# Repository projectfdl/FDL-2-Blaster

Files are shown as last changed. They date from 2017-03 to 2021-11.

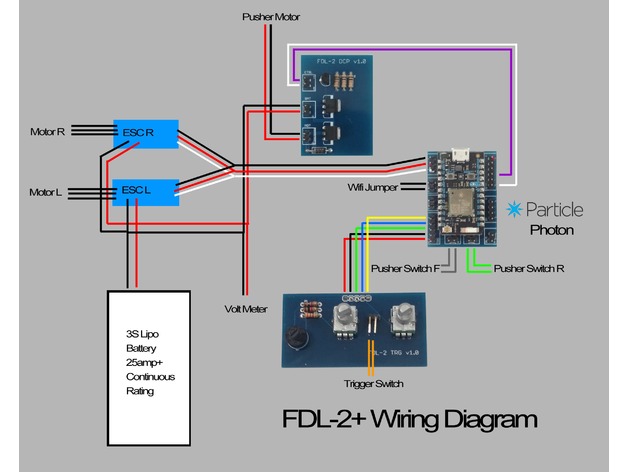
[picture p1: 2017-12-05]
FDL-2+/FDL-2+_Wiring_Diagram.jpg

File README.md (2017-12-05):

# FDL-2-Blaster

This is the Git repository for all things FDL-2 related. You can find all the print/STL files you need here to print your own FDL-2 as well as parts lists, wiring diagrams and firmware.

There are technically three versions of the FDL-2. The original FDL-2 with a stepper pusher motor, the FDL-2+ with the DC pusher motor, and the FDL-2X with the OLED screen and click knob.

If you are building an FDL-2+:

If you are building an FDL-2X:

If you are building an FDL-2 Original Stepper version:

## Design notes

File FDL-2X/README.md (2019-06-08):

# FDL-2X-Blaster

To update FDL-2X firmware you need the following:

[Sparkfun Microview Programmer](https://www.sparkfun.com/products/12924)<br/>
[XLoader](http://xloader.russemotto.com/)<br/>
Windows computer. (There are ways to do this on a mac but I have not found a quick and easy utility to do so)<br/>
<br/>
#### Flashing your FDL-2X</br>
#### Caution!!! Flash your blaster at your own risk. Doing so is not covered by any sort of warranty. If you are not comfortable or 100% confident, consider sending your Microview to Project FDL to flash.</br>
-Remove the rear blaster cap and Microview. <br/>
-Insert the Microview programmer into the USB port on your Windows computer. <br/>
-Insert the Microview from your blaster into the programmer paying careful attention to orientation.<br/>
-The screen on your microview should point up with the USB connector facing left. There is a picture indication on the board as well.<br/>
-Run XLoader. <br/>
-Choose your desired firmware hex file. <br/>
-Select the Duemilanove/Nano(ATmega328) option under device.<br/>
-Choose the com port of your USB programmer.<br/>
-Set baud rate to 115200.<br/>
-Click upload.<br/>
-You should see the lights under the screen flickering. Flashing can take 30 seconds or longer.<br/>
-When flashing is complete you will see the FDL-2X splash screen then the speed menu as usual.<br/>
-Remove the Microview from the programmer and put it back in your FDL-2X.<br/>
-Replace the rear cap and you're good to go.<br/>

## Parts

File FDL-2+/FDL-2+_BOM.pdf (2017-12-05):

# FDL-2+ BOM

Item | Quantity | Model

Major Components
Brushless Motor | 2 | Multistar Elite 2204-2300KV
ESC | 2 | Afro ESC 12Amp BEC UltraLite Multirotor ESC V3 (SimonK Firmware)
Photon | 1 | Particle Photon wHeaders
20A power switch | 1 | Digikey EG4777-ND
Pot Knob | 2 | Digikey 450-1736-ND
Volt Meter | 1 | 0.36" Volt Meter
25D Gear Motor | 1 | https://www.pololu.com/product/3202
Trigger Button | 1 | Digikey EG1938-ND
Microswitch (Pusher F&R) | 2 | Digikey P10864S-ND

Hardware
6-32 Machine Screw 3/8 | 29
6-32 Machine Screw 1/2 | 18
6-32 Machine Screw 3/4 | 2
6-32 Machine Screw 1 | 3
10-32 Set Screw 1/4 | 1
#10 washer | 1

M3x8 Hex Screw | 9
M2x5 Csnk Hex Screw | 9
M3x6 Csnk Hex Screw | 3
Spring from ballpoint pen | 1

DCP PCB
PCB DCP | 1 | FDL-2 DCP V1.0
N Channel Mosfet | 1 | Digikey IRLU3410PBF-ND
P Channel Mosfet | 1 | Digikey IRFU5505PBF-ND
NPN Transistor | 1 | Digikey 2N4401-ND
Flyback Diode | 1 | Digikey UF4007CT-ND
Header Male 2p | 3
Resistor 10k | 3

Control PCB
PCB Control | 1 | FDL-2 CTL V1.1
Header Fem 12p | 2
Header Male 2p | 5
Header Male 3p | 1
Header Male 4p | 2
Header Male 6p | 1

Trigger PCB
PCB Trigger/Speed | 1 | FDL-2 TRG v1.1
Rotary Switch | 1 | Digikey CKN10699-ND
Potentiometer | 2 | Digikey PTV09A-4020F-B103-ND
Header Male 2p RgtAng | 1
Header Male 5p | 1
Resistor 1k | 2
Resistor 3.3k | 1

# FDL-2+ BOM

Item | Quantity | Model
ESC Control
M-F Y Splitter Servo Cable | 1

Power Distro/ESC Bundle
3.5mm bullet conn male | 1
Female Tab Conn 1/4 12ga | 1
JR Conn Male & shell | 1

Battery Adapter
XT60 conn male | 1
3.5mm bullet conn female | 1
Female Tab Conn 1/4 16ga | 1
16ga high strand silicon wire red/blk

Notes
Use 16ga silicon wire for battery connections, 22ga silicon wire for pusher motor and volt meter connections
Use 24-26ga color coded wires for all digital signal wiring
It is up to you how you choose to connect components to the PCB's. Choose simple slide connectors and crimp pins, JST connectors, or solder directly to the boards

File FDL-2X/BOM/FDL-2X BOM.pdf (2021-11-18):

# FDL-2X BOM

Item | Quantity | Model

Major Components
Brushless Motor | 2 | Multistar Elite 2204-2300KV
ESC | 2 | Afro ESC 20Amp BEC Race Spec ESC (SimonK Firmware)
MicroView | 1 | Sparkfun Microview OLED/Arduino Combo
25D Gear Motor | 1 | https://www.pololu.com/product/3202
Trigger Button | 1 | Digikey EG1938-ND
Microswitch (Pusher F&R) | 2 | Digikey P10864S-ND

Hardware
6-32 Machine Screw 3/8 | 33
6-32 Machine Screw 1/2 | 18
6-32 Machine Screw 3/4 | 2
6-32 Machine Screw 1 | 3
10-32 Set Screw 1/4 | 1
#10 washer | 1

M3x8 Hex Screw | 9
M2x5 Csnk Hex Screw | 9
M3x6 Csnk Hex Screw | 3
Spring from ballpoint pen | 1
Right angle m-m pin header (2 pin ) | 1

DCP PCB
PCB DCP | 1 | FDL-2 DCP V1.2
N Channel Mosfet | 1 | Digikey IRLU3410PBF-ND
P Channel Mosfet | 1 | Digikey IRFU5505PBF-ND
NPN Transistor | 1 | Digikey 2N4401-ND
Flyback Diode | 1 | Digikey UF4007CT-ND
Header Male 2p | 3
Resistor 10k | 3

Control PCB
PCB Control | 1 | FDL-2X CTL V1.1
Header Fem 8p | 2
Resistor 1k | 1
Resistor 10k | 1
Resistor 100k | 1
Tactile Switch | 1 | Digikey 450-1643-ND
Rotory Encoder | 1 | Digikey PEC11R-4215K-S0024-ND
Buzzer | 1 | Digikey 102-1152-ND
NPN Transistor | 1 | Digikey 2N4401-ND
Header Male 2p | 5
Header Male 3p | 1

ESC Control
M-F Y Splitter Servo Cable | 1

Power Distro/ESC Bundle
3.5mm bullet conn male | 1
Female Tab Conn 1/4 12ga | 1
JR Conn Male & shell | 1

Battery Adapter
XT60 conn male | 1
3.5mm bullet conn female | 1
Female Tab Conn 1/4 16ga | 1
16ga high strand silicon wire red/blk

Notes

# FDL-2X BOM

Item | Quantity | Model
Use 16ga silicon wire for battery connections, 22ga silicon wire for pusher motor and volt meter connections
Use 24-26ga color coded wires for all digital signal wiring
It is up to you how you choose to connect components to the PCB's. Choose simple slide connectors and crimp pins, JST connectors, or solder directly to the boards

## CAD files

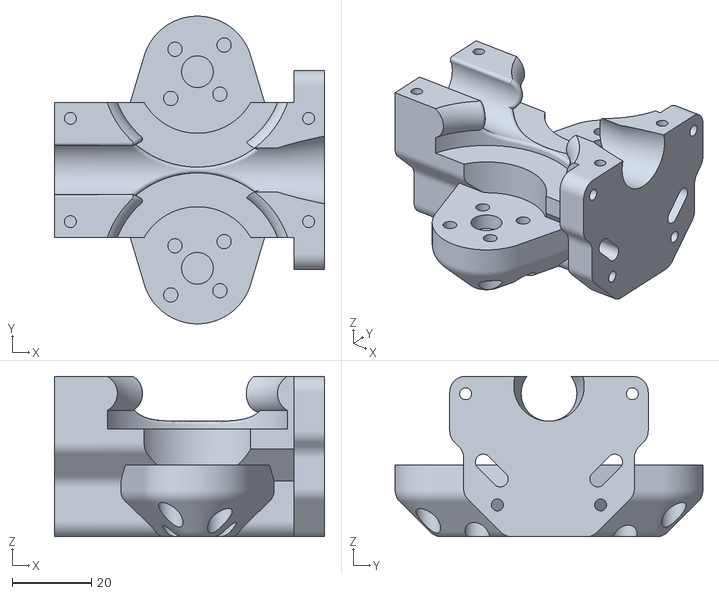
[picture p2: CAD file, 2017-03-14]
FDL-2 Core/STL/FDL-2_Barrel_Main.stl
68.0 x 77.5 x 40.4

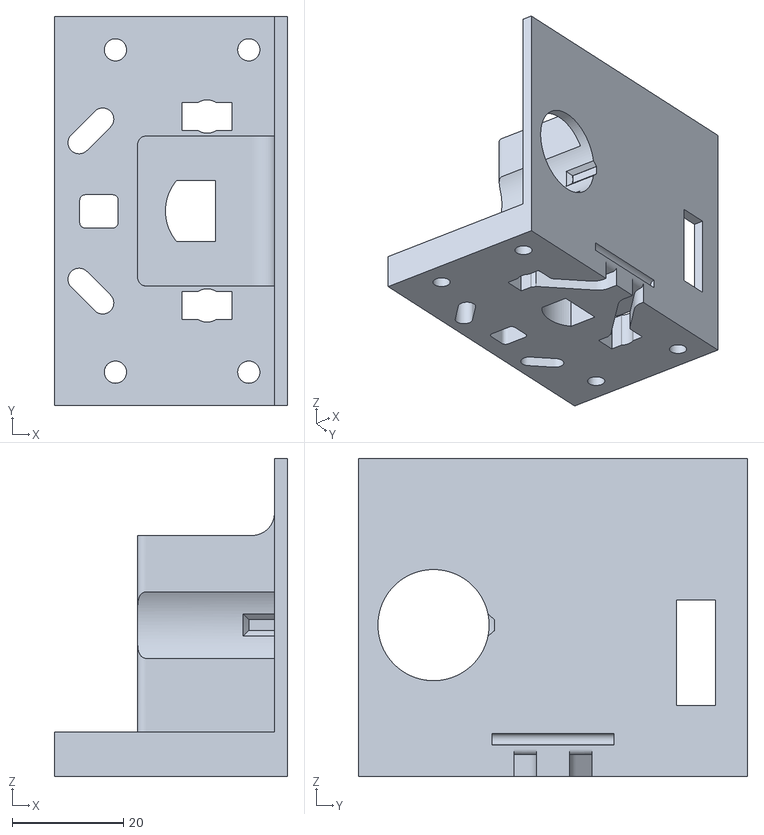
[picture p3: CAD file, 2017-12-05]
FDL-2 Core/STL/FDL-2_Pusher_Guide.stl
42.0 x 70.0 x 57.3

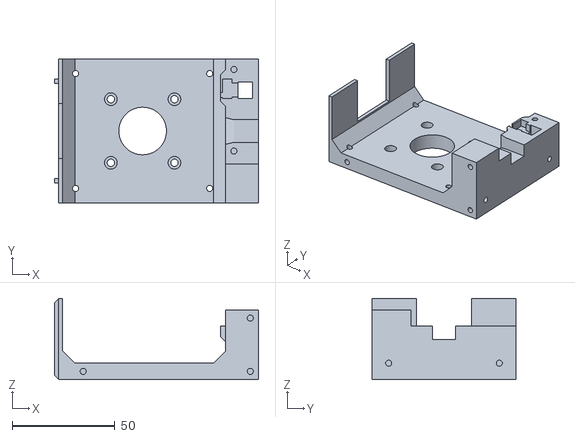
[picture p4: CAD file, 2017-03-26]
FDL-2 Stepper/STL/FDL-2_Rear_Plate.stl
99.5 x 70.0 x 39.6

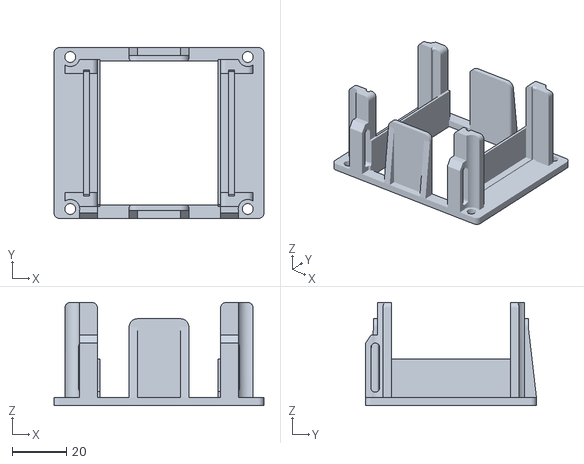
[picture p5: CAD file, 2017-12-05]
FDL-2+/STL/FDL-2+_PCB_Mount.stl
77.4 x 63.0 x 38.0

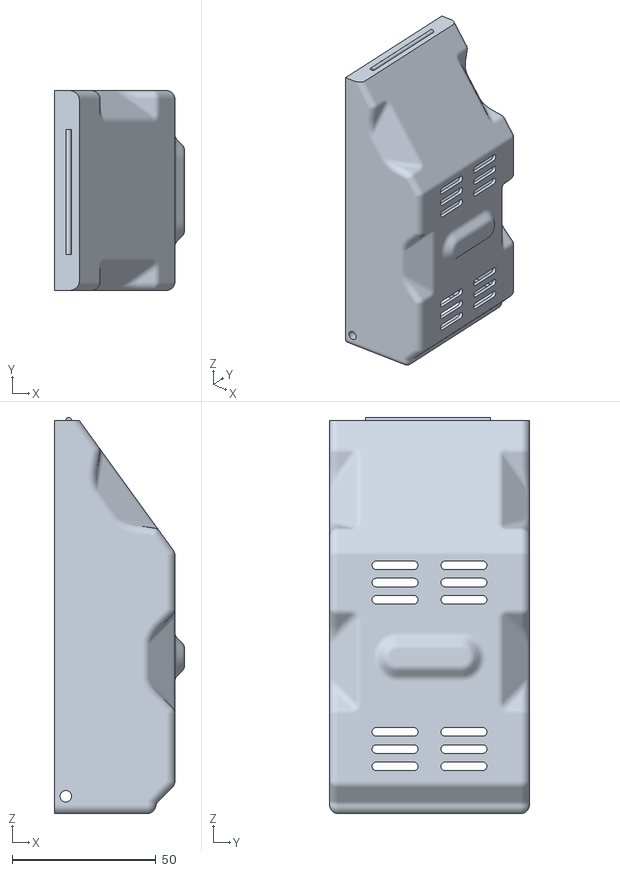
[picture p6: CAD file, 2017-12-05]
FDL-2X/STL/FDL-2X_Electronics_Cover.stl
45.4 x 69.6 x 137.9

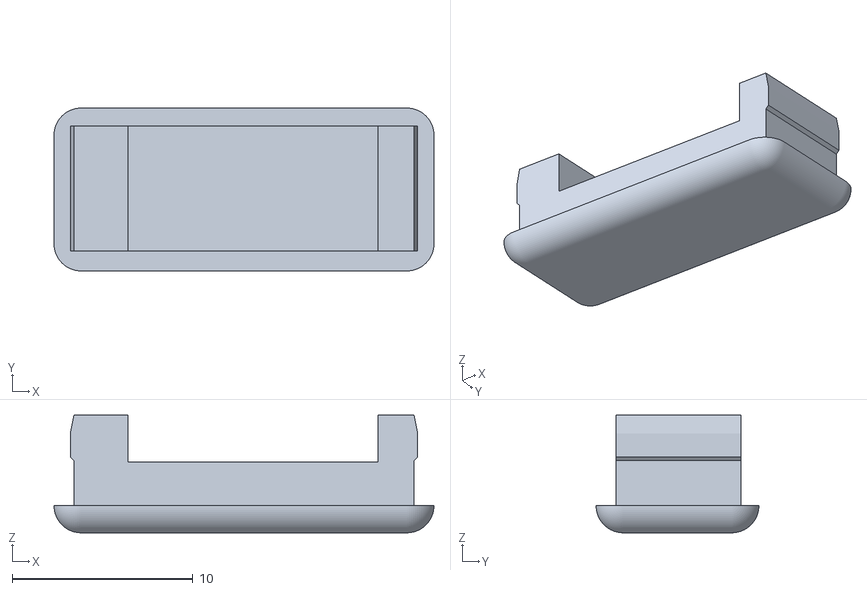
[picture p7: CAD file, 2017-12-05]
FDL-2 Core/STL/FDL-2_Pusher_Guide_Switch_Insert.stl
21.0 x 9.00 x 6.50

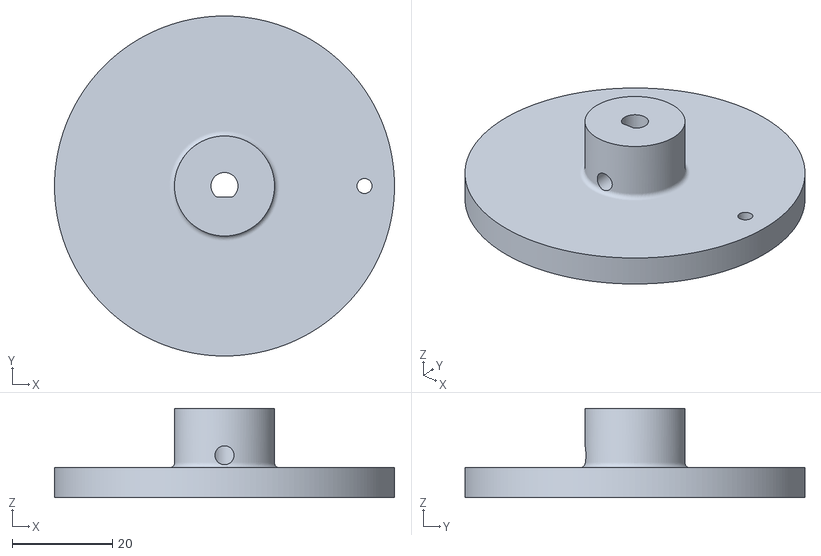
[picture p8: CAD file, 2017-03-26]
FDL-2 Stepper/STL/FDL-2_Spinner.stl
68.0 x 68.0 x 17.9

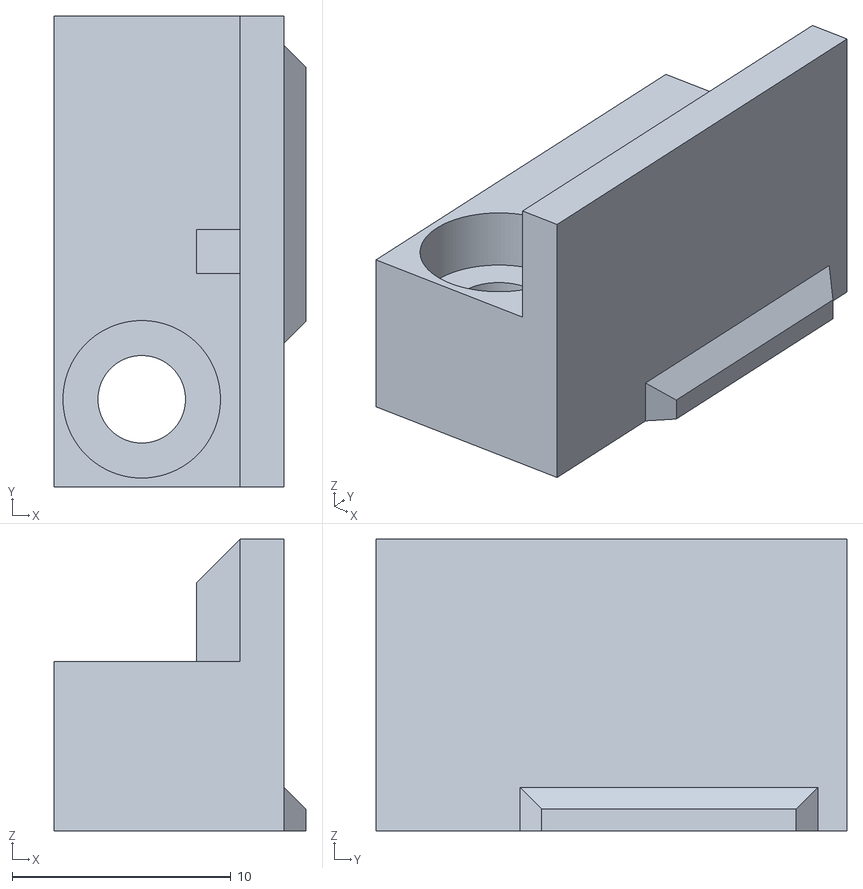
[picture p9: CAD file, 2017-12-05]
FDL-2+/STL/FDL-2+_Rear_Plate_Cap_Front.stl
11.5 x 21.5 x 13.4

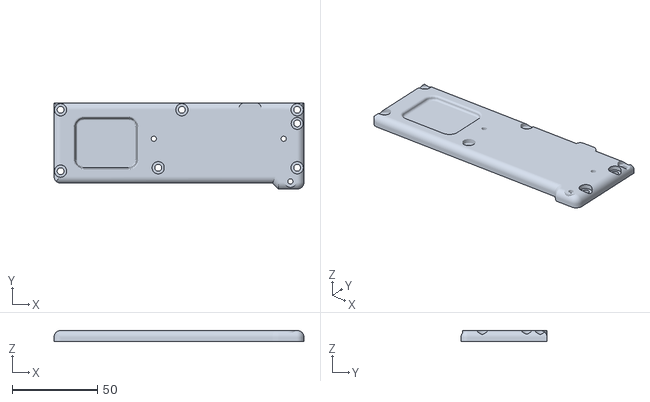
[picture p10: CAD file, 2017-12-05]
FDL-2X/STL/FDL-2X_Panel_Right.stl
146.6 x 50.5 x 6.50

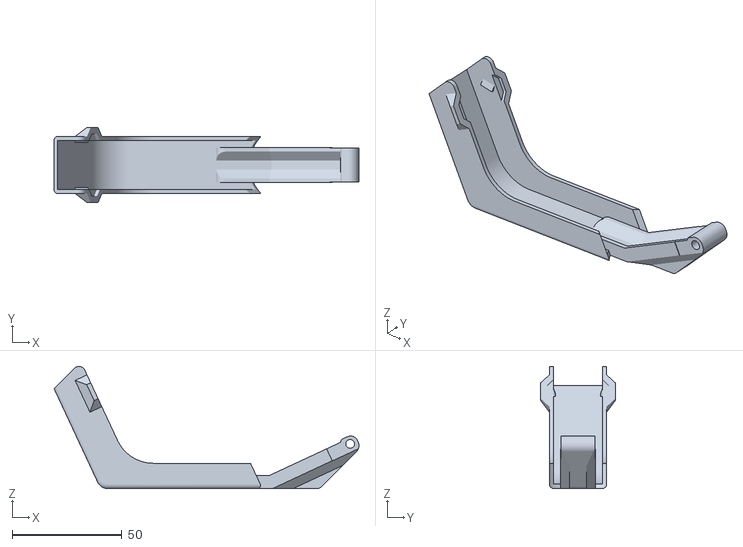
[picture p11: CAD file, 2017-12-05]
FDL-2 Core/STL/FDL-2_Handle_Guard_Outer.stl
139.2 x 34.1 x 55.7

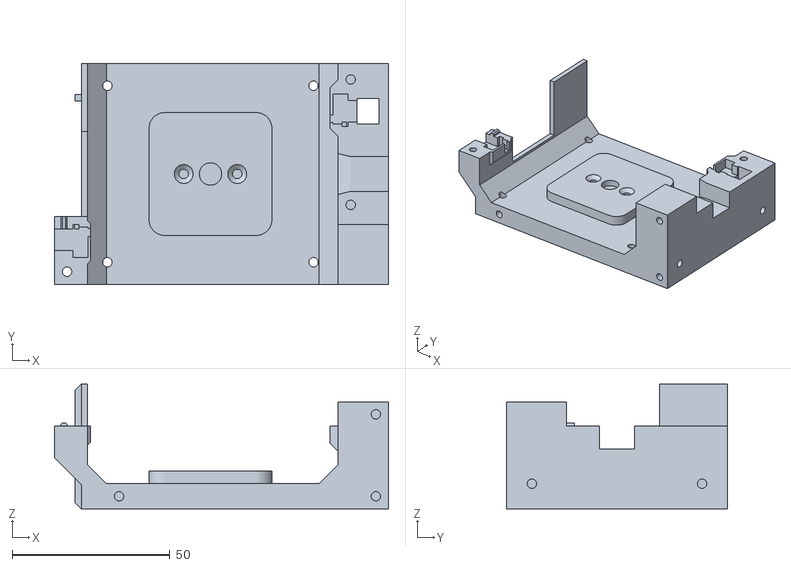
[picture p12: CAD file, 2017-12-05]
FDL-2+/STL/FDL-2+_Rear_Plate.stl
106.0 x 70.0 x 39.6

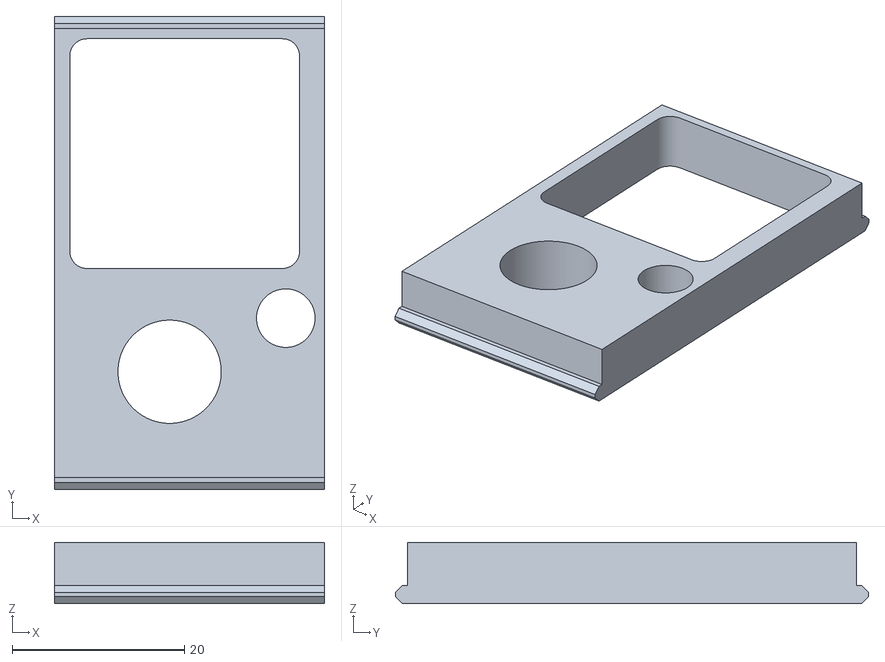
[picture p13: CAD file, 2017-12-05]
FDL-2X/STL/FDL-2X_Screen_Plate.stl
31.4 x 55.0 x 7.10

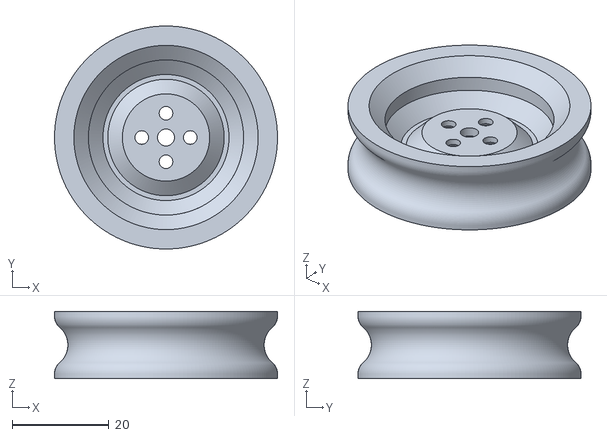
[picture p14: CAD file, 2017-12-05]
FDL-2 Core/STL/FDL-2_Flywheel_x2_9.5mm_dia_0.5mm_crush.stl
46.0 x 46.0 x 13.8

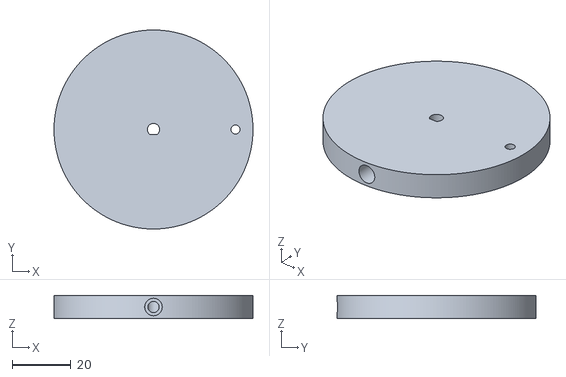
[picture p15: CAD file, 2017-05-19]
FDL-2+/STL/FDL-2+_Spinner.stl
68.0 x 68.0 x 8.00

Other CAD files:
FDL-2X/STL/FDL-2X_Panel_Right_Cap.stl
FDL-2+/STL/FDL-2+_Electronics_Cover.stl
FDL-2X/STL/FDL-2X_Counter_Reset_Button.stl
FDL-2 Core/STL/FDL-2_Barrel_Cap.stl
FDL-2 Core/STL/FDL-2_ESC_Wire_Cap_L.stl
FDL-2 Core/STL/FDL-2_ESC_Wire_Cap_R.stl
FDL-2 Core/STL/FDL-2_Handle.stl
FDL-2 Core/STL/FDL-2_Handle_Guard_Inner.stl
FDL-2 Core/STL/FDL-2_Mag_Release_Block.stl
FDL-2 Core/STL/FDL-2_Mag_Release_Catch.stl
FDL-2 Core/STL/FDL-2_Mag_Release_Post.stl
FDL-2 Core/STL/FDL-2_Magwell.stl
FDL-2 Core/STL/FDL-2_Magwell_Cap.stl
FDL-2 Core/STL/FDL-2_Magwell_Insert_Blank.stl
FDL-2 Core/STL/FDL-2_Pusher.stl
FDL-2 Core/STL/FDL-2_Rail_Top.stl
FDL-2 Core/STL/FDL-2_Rear_Plate.stl
FDL-2 Core/STL/FDL-2_Rear_Plate_Cap_Rear.stl
FDL-2 Core/STL/FDL-2_Spinner_Bushing.stl
FDL-2 Core/STL/FDL-2_Stock_Att.stl
FDL-2+/STL/FDL-2+_Mode_Knob.stl
FDL-2+/STL/FDL-2+_Nameplate.stl
FDL-2+/STL/FDL-2+_Panel_Left.stl
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

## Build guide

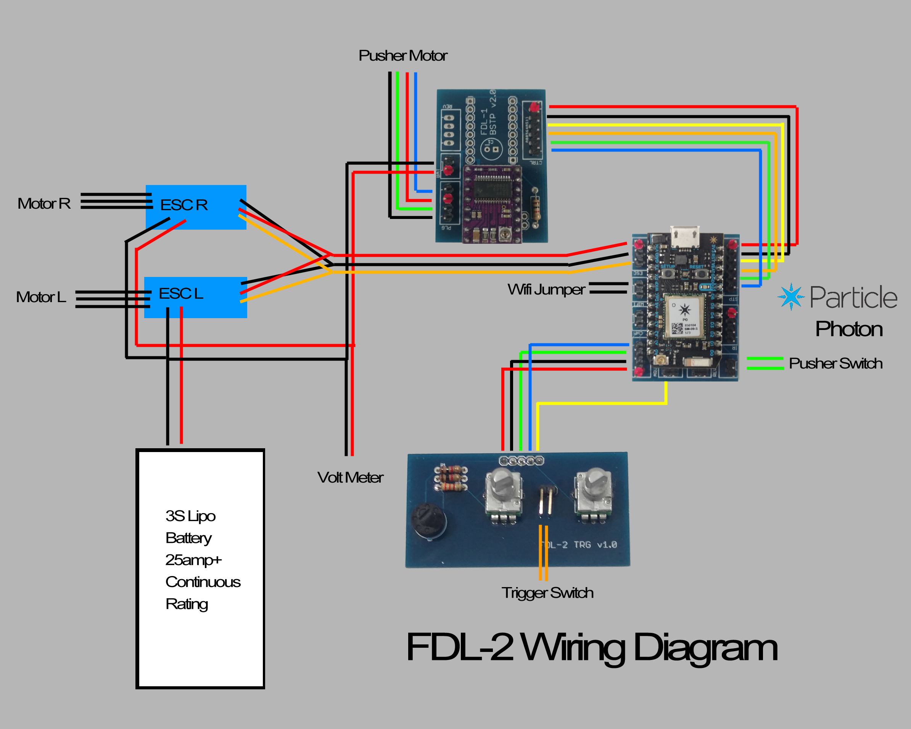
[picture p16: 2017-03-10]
FDL-2 Stepper/FDL-2_Stepper_Wiring Diagram.png

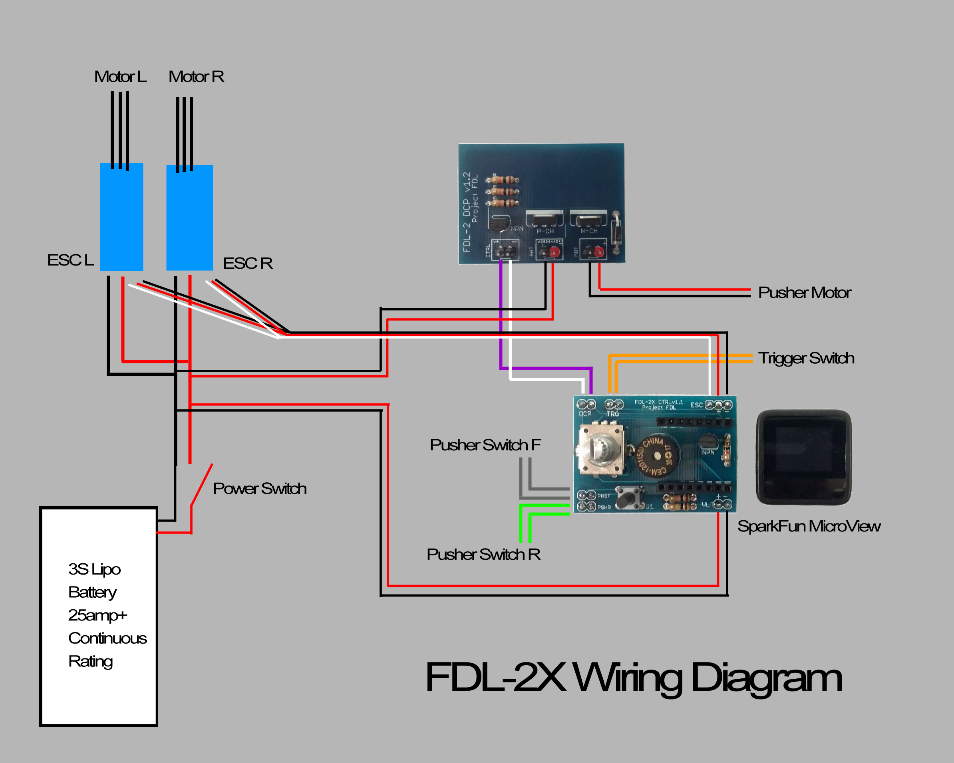
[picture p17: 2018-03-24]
FDL-2X/FDL-2X-Wiring-Diagram.png

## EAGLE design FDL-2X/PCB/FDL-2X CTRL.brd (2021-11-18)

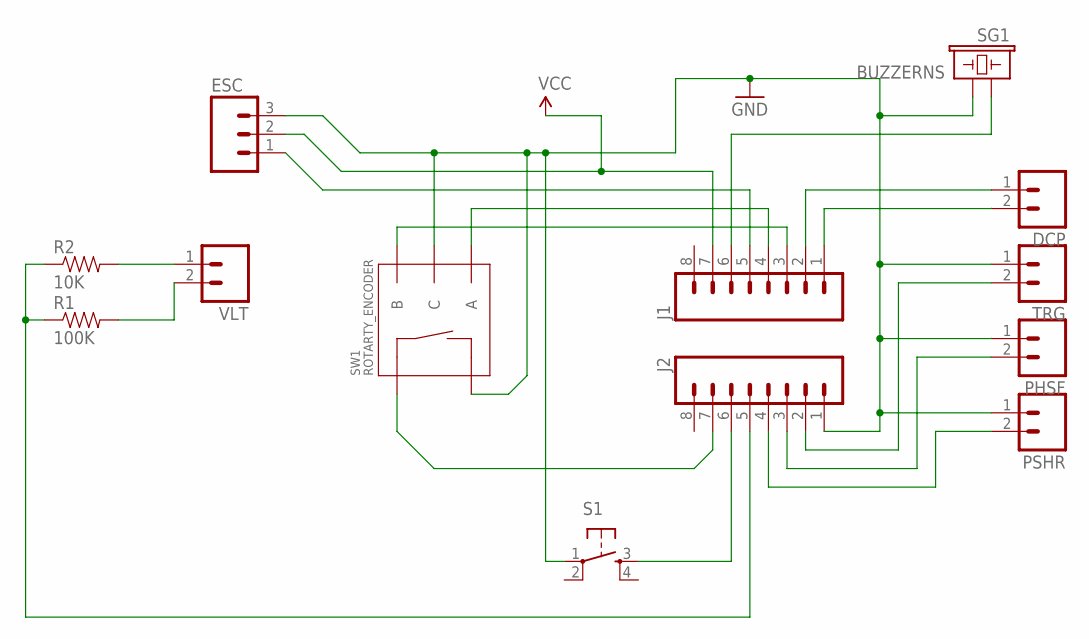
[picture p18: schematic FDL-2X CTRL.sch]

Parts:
DCP: M02PTH; 1X02
ESC: M03PTH; 1X03
J1, J2: M08SILK_FEMALE_PTH; 1X08
PHSF: M02PTH; 1X02
PSHR: M02PTH; 1X02
R1: 100K; AXIAL-0.3
R2: 10K; AXIAL-0.3
S1: TAC_SWITCHPTH; TACTILE-PTH
SG1: BUZZERNS; BUZZER-12MM-NS
SW1: ROTARTY_ENCODER; ROTARY_ENC_PLAIN
TRG: M02PTH; 1X02
VLT: M02PTH; 1X02

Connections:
GND: ESC.3, J2.1, PHSF.1, PSHR.1, S1.1, SG1.- (2), SW1.C, SW1.SW-, TRG.1
unnamed: ESC.1, J1.5
unnamed: J2.6, S1.3
unnamed: J2.2, TRG.2
unnamed: J2.3, PHSF.2
unnamed: J2.7, SW1.SW+
unnamed: J2.4, PSHR.2
unnamed: J1.4, SW1.A
unnamed: J1.3, SW1.B
unnamed: DCP.1, J1.2
unnamed: R2.P$2 (2), VLT.1
unnamed: DCP.2, J1.1
unnamed: R1.P$2 (2), VLT.2
unnamed: J1.6, SG1.+ (1)
unnamed: J2.5, R1.P$1 (1), R2.P$1 (1)
VCC: ESC.2, J1.7

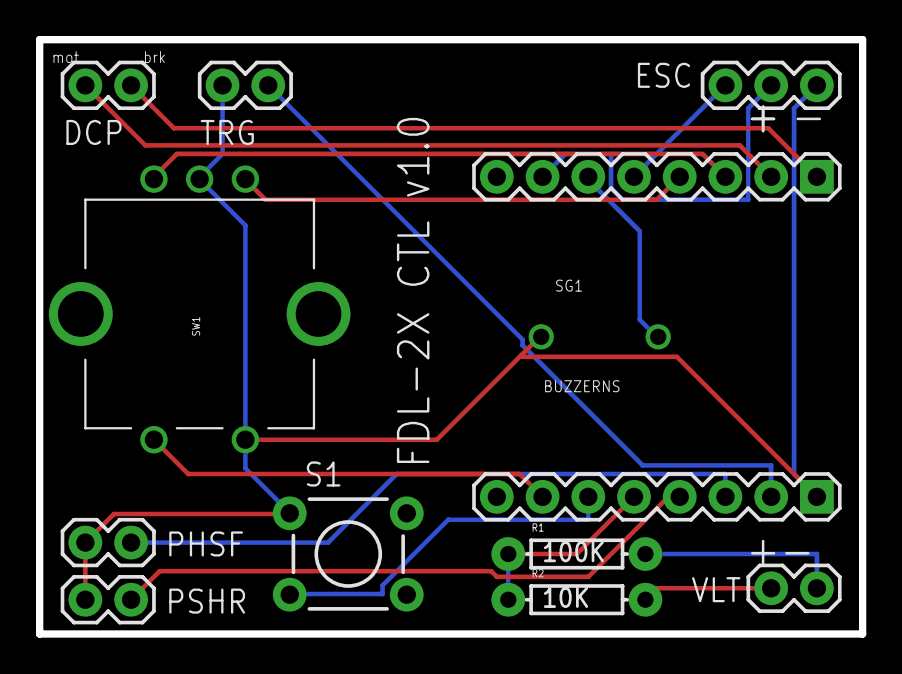
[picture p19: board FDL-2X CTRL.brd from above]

Board: 2 copper layers, 45.7 x 33.0 mm, 13 parts (0 on the bottom side), 16 nets.

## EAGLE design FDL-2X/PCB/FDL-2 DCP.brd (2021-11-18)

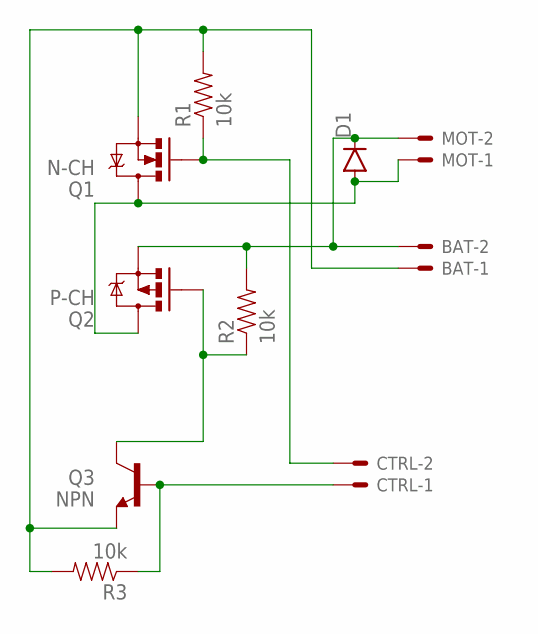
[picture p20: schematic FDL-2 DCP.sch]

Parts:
BAT: JST-XH-02-PIN-LONG-PAD; JST-XH-02-PACKAGE-LONG-PAD
CTRL: JST-XH-02-PIN-LONG-PAD; JST-XH-02-PACKAGE-LONG-PAD
D1: DIODEPTH; DIODE-1N4001
MOT: JST-XH-02-PIN-LONG-PAD; JST-XH-02-PACKAGE-LONG-PAD
Q1: N-CH; TO220V
Q2: P-CH; TO220V
Q3: NPN; TO-92
R1, R2, R3: 10k; AXIAL-0.3EZ

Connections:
unnamed: CTRL.1, Q3.2 (B), R3.P$1 (1)
unnamed: Q2.1 (G), Q3.3 (C), R2.P$1 (1)
unnamed: BAT.1, Q1.3 (S), Q3.1 (E), R1.P$2 (2), R3.P$2 (2)
unnamed: CTRL.2, Q1.1 (G), R1.P$1 (1)
unnamed: BAT.2, D1.C, MOT.2, Q2.3 (S), R2.P$2 (2)
unnamed: D1.A, MOT.1, Q1.2 (D), Q2.2 (D)

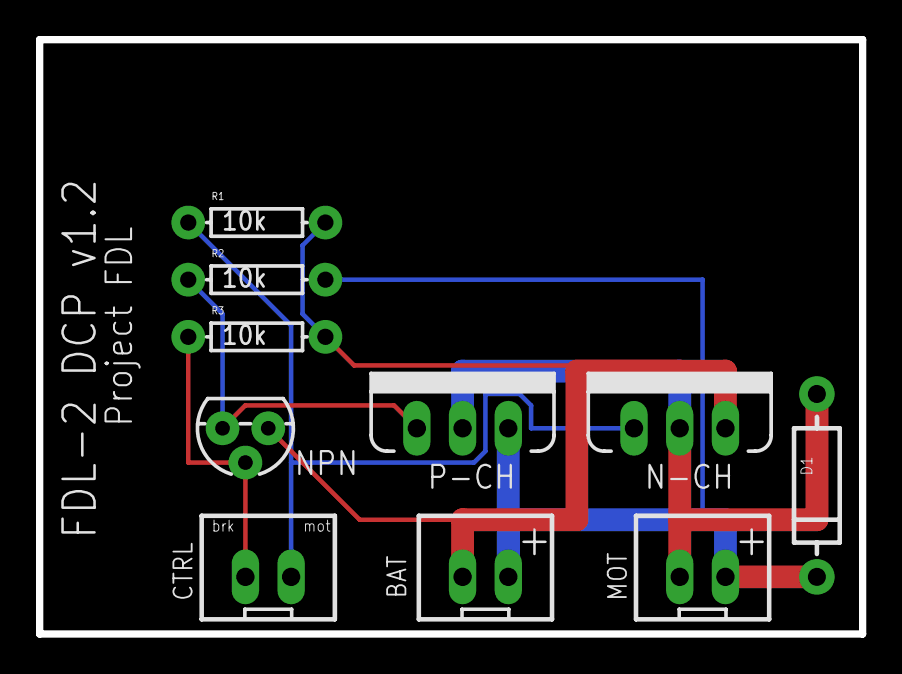
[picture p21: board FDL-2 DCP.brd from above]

Board: 2 copper layers, 45.7 x 33.0 mm, 10 parts (0 on the bottom side), 6 nets.

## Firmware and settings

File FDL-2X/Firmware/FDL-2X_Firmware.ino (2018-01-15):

#include <MicroView.h>
#include <Encoder.h>
#include <Servo.h>
#include <EEPROM.h>

Encoder myEnc(2, 3);
Servo flywheelESC; 

//PINS
int pusherBrakePin = 0;
int pusherEnablePin = 1;
int escPin = 5;
int buzzerPin = 6;
int triggerPin = A0;
int pusherSwitchFPin = A1;
int pusherSwitchRPin = A2;
int voltMeterPin = A3;
int resetBtnPin = A4;
int menuBtnPin = A5;

//MENUS
#define batteryCheckLength 6
float batteryCheck[batteryCheckLength];
unsigned long lastBatteryCheck = 0;
unsigned long batteryCheckDelay = 300;
int batteryCheckIndex = 0;
float batteryCheckSum = 0.0;

#define knobMenuLength 12
String knobMenuArray[knobMenuLength] = 
{
  "Speed  ",
  "ROF    ",
  "Burst  ",
  "Counter", 
  "MinSpin",
  "MaxSpin", 
  "MinSpd ",
  "MaxSpd ",
  "Load   ",
  "Save   ",
  "Bright ",
  "Sound "
};
int knobMenuIndex = 0;

#define burstMenuLength 4
String burstMenuArray[burstMenuLength] = {"1","2","3","F"};
int burstMenuIndex = 0;

#define soundMenuLength 2
String soundMenuArray[soundMenuLength] = {"ON ","OFF"};
int soundMenuIndex = 0;

#define presetMenuLength 4
String presetMenuArray[presetMenuLength] = {"Back"," 1  "," 2  "," 3  "};
int presetMenuIndex = 0;



MicroViewWidget *mainGauge;
MicroViewWidget *voltMeter;

int versionNumber = 1;

int speedValue = 50;
int rofValue = 100;
int counterValue = 0;
int magSizeValue = 18;
int brightnessValue = 100;
int minSpeedValue = 0;
int maxSpeedValue = 100;

int minSpinupValue = 300;
int maxSpinupValue = 180;

bool liveKnobScrollMode = false;
bool countResetWasDown = false;
bool menuBtnWasDown = false;
bool firstMenuRun = true;

bool speedLockedOut = false;

bool firstRun = true;

unsigned long lastTriggerUp = 0;
unsigned long lastSettingsSave = 0;
unsigned long lastBatAlarm = 0;

long encoderChange = 0;

float vPow = 5.12; //5.27
float r1 = 100000;
float r2 = 10000;

struct BlasterSettings {
  int versionNumber;
  int speedValue;
  int rofValue;
  int burstCount;
  int minSpinupValue;
  int maxSpinupValue;
  int minSpeed;
  int maxSpeed;
  int brightness;
  bool soundOn;
  int magSize;
};
BlasterSettings currentSettings = { 1, 80, 100, 1, 300, 180, 0, 100, 100, true, 18 }; 

BlasterSettings presets[4] = 
{
  { 1, 80, 100, 1, 300, 180, 0, 100, 100, true, 18 },
  { 1, 30, 50, 1, 300, 180, 0, 50, 0, true, 6 },
  { 1, 50, 100, 3, 300, 180, 0, 70, 50, false, 12 },
  { 1, 80, 100, 2, 300, 180, 0, 100, 100, true, 18 }
};


void setup() {

  flywheelESC.attach(escPin); 
  flywheelESC.writeMicroseconds(1000);
  
  uView.begin();// start MicroView
  uView.clear(PAGE);// clear page
  uView.display();

  pinMode(voltMeterPin, INPUT);
  
  pinMode(menuBtnPin, INPUT_PULLUP);
  pinMode(resetBtnPin, INPUT_PULLUP);
  pinMode(triggerPin, INPUT_PULLUP);
  pinMode(pusherSwitchFPin, INPUT_PULLUP);
  pinMode(pusherSwitchRPin, INPUT_PULLUP);

  pinMode(pusherEnablePin, OUTPUT);
  pinMode(pusherBrakePin, OUTPUT);
  pinMode(buzzerPin, OUTPUT);

  //uView.drawBitmap(bitmapTest);
  //uView.display();

  renderSplash();

  mainGauge = new MicroViewGauge(16,30,0,100,WIDGETSTYLE0 + WIDGETNOVALUE);
  voltMeter = new MicroViewSlider(56, 14, 109, 126, WIDGETSTYLE2 + WIDGETNOVALUE);

  mainGauge->reDraw();
  voltMeter->reDraw();
  
  initSettings();
  loadSettings(0);

  //init battery average read values
  for(int x = 0; x < batteryCheckLength; x++){
    batteryCheck[x] = 12.0;
  }
  lastBatteryCheck = millis();
  batteryCheckSum = 12.0 * batteryCheckLength;
  
  renderScreen();
  delay(350);
  
  tone(6, 2000, 350);

  if(counterResetDown()){
    delay(500);

    tone(6, 3000, 200);
    delay(300);
    tone(6, 3000, 200);

    speedLockedOut = true;
  }
}


void loop() {

  //check for trigger
  if(triggerDown()){
    fireSequence();
  }
  else{
    flywheelESC.writeMicroseconds(1000);
  }

  //check for counter reset
  if(counterResetDown() && !speedLockedOut){
    if(!countResetWasDown){
      counterValue = magSizeValue;
    }
    countResetWasDown = true;
  }
  else{
    countResetWasDown = false;
  }
  
  renderScreen();

  if(lastSettingsSave != 0 && millis() - lastSettingsSave < 1000){
     //don't save
  }
  else{
     writeSettings(0);
     lastSettingsSave = millis();
  }
  
}

void writeSettings(int presetNumber){

  if((currentSettings.versionNumber != versionNumber||
  currentSettings.speedValue != speedValue ||
  currentSettings.rofValue != rofValue ||
  currentSettings.burstCount != getBurstCount() ||
  currentSettings.minSpinupValue != minSpinupValue ||
  currentSettings.maxSpinupValue != maxSpinupValue ||
  currentSettings.minSpeed != minSpeedValue ||
  currentSettings.maxSpeed != maxSpeedValue ||
  currentSettings.magSize != magSizeValue ||
  currentSettings.brightness != brightnessValue ||
  currentSettings.soundOn != (soundMenuIndex == 0)) ||
  presetNumber > 0){
    currentSettings = { 
      versionNumber, 
      speedValue,
      rofValue,
      getBurstCount(),
      minSpinupValue,
      maxSpinupValue,
      minSpeedValue,
      maxSpeedValue,
      brightnessValue,
      soundMenuIndex == 0,
      magSizeValue};

    int memLoc = presetNumber * 100;
      
    EEPROM.put(memLoc, currentSettings);
    //if(soundMenuIndex == 0){
    //  tone(6,3000,50);
    //}
  }
}

void loadSettings(int presetNumber){

  int memLoc = presetNumber * 100;
  EEPROM.get(memLoc, currentSettings);
    
  //if EEPROM empty all values will come back -1
  if(currentSettings.versionNumber == -1 || currentSettings.versionNumber != versionNumber){
      currentSettings = { 1, 80, 100, 1, 300, 150, 0, 100, 100, true, 18 };
  }
  
  speedValue = currentSettings.speedValue;
  rofValue = currentSettings.rofValue;
  
  int readBurst = constrain(currentSettings.burstCount, 1, 4);
  burstMenuIndex = readBurst - 1;
  
  minSpinupValue = currentSettings.minSpinupValue;
  maxSpinupValue = currentSettings.maxSpinupValue;
  minSpeedValue = currentSettings.minSpeed;
  maxSpeedValue = currentSettings.maxSpeed;
  magSizeValue = currentSettings.magSize;
  brightnessValue = currentSettings.brightness;

  if(presetNumber == 0){
    soundMenuIndex = currentSettings.soundOn ? 0 : 1;
  }
  
}

void savePreset(int presetIndex){

  writeSettings(presetIndex);
  
  tone(6, 2000, 50);
  delay(100);
  tone(6, 2000, 100);
  
}

void loadPreset(int presetIndex){

  loadSettings(presetIndex);
  
  tone(6, 4000, 50);
  delay(100);
  tone(6, 4000, 100);
  
}

void initSettings(){

  BlasterSettings initTestStruct;

  for(int i = 0; i < 4; i++){

    int memLoc = i * 100;
    
    EEPROM.get(memLoc, initTestStruct);
    
    ////if EEPROM empty all values will come back -1
    if(initTestStruct.versionNumber == -1){
        initTestStruct = presets[i];
        EEPROM.put(memLoc, initTestStruct);
    }
  }
}


bool fireSequence(){
    
    long currMills = millis();
    
    int kickonSpeed = readESCPower();
    //flywheelESC.write(kickonSpeed); 
    flywheelESC.writeMicroseconds(kickonSpeed);

    int spinupDelay = getSpinup();

    //tone(6, 3000);
    
    if(lastTriggerUp != 0 && millis() - lastTriggerUp < 1000){
       delay(10);
    }
    else{
       delay(spinupDelay); 
    }

    //noTone(6);
    
    int burstCount = getBurstCount();

    long counter = 0;
    
    while(burstCount > 1 && triggerDown()){
        
        int burstBreakDelay = map(rofValue, 0, 100, 100, 0);
        
        counter = 50;
        while(digitalRead(pusherSwitchFPin) == HIGH && counter > 0){
            digitalWrite(pusherEnablePin, HIGH);
            delay(6);
            counter--;
        }
        
        counter = 50;
        while(digitalRead(pusherSwitchFPin) == LOW && counter > 0){
            digitalWrite(pusherEnablePin, HIGH);
            delay(6);
            counter--;
        }
        
        burstCount--;
        
        if(burstBreakDelay > 5){
            digitalWrite(pusherEnablePin, LOW);
            delayMicroseconds(200);
            digitalWrite(pusherBrakePin, HIGH);
            delay(burstBreakDelay);
            digitalWrite(pusherBrakePin, LOW);
            delayMicroseconds(200);
        }
        
        counterValue--;
        counterValue = max(counterValue, 0);
        renderScreen();
    }

    //tone(6, 4000);

    counter = 50;
    while(digitalRead(pusherSwitchFPin) == HIGH && counter > 0){
      digitalWrite(pusherEnablePin, HIGH);
      delay(5);
      counter--;
    }
    
    digitalWrite(pusherEnablePin, LOW);
    
    delayMicroseconds(500);
    
    digitalWrite(pusherBrakePin, HIGH);
    delay(30);
    digitalWrite(pusherBrakePin, LOW);
    
    delayMicroseconds(500);

    digitalWrite(pusherEnablePin, HIGH);
    delayMicroseconds(16000);
    digitalWrite(pusherEnablePin, LOW);
    
    counter = 1000;
    while(digitalRead(pusherSwitchRPin) == HIGH && counter > 0){
        delayMicroseconds(200);
        counter--;
    }
    
    digitalWrite(pusherEnablePin, LOW);
    flywheelESC.writeMicroseconds(1000);

    delayMicroseconds(200);
    
    digitalWrite(pusherBrakePin, HIGH);
    delay(30);
    digitalWrite(pusherBrakePin, LOW);
    
    delayMicroseconds(200);

    counterValue--;
    counterValue = max(counterValue, 0);

    int toneFreq = 4000;

    renderScreen();
    
    while(triggerDown()){};
    
    lastTriggerUp = millis();
    
    //noTone(6);
    
    return true;
}

boolean triggerDown(){
  return digitalRead(triggerPin) == LOW;
}

boolean counterResetDown(){
  return digitalRead(resetBtnPin) == LOW;
}

int readESCPower(){
  return map(speedValue, 0, 100, 1285, 1860);
}

int getSpinup(){
  return map(speedValue, 0, 100, minSpinupValue, maxSpinupValue);
}

int getBurstCount(){
  if(burstMenuIndex >= burstMenuLength - 1){
    return 100;
  }
  else{
    return burstMenuIndex + 1;
  }
}

int getROF(){
  return rofValue;
}


/////////////
///RENDER
/////////////
void renderScreen(){

  int contrastValue = map(brightnessValue, 0, 100, 0, 255);
  uView.contrast(contrastValue);

  if(speedLockedOut){
    renderLockIndicator();
  }
  else{
    renderCounter();
  }
  
  renderVoltMeter();
    
  if(liveKnobScrollMode){
    renderKnobScrollMenu();
  }
  else{
    switch(knobMenuIndex){
      case 0:
        renderGauge(speedValue, "Speed", 0, 100, minSpeedValue, maxSpeedValue);
        break;
      case 1:
        renderGauge(rofValue, "ROF", 0, 100, 0, 100);
        break;
      case 2:
        renderBurstMenu();
        break;
      case 3:
        renderCounterMenu();
        break;
      case 4:
        if(!speedLockedOut){
          renderGauge(minSpinupValue, "Spn Min", 100, 500, 100, 500);
        }
        break;
      case 5:
        if(!speedLockedOut){
          renderGauge(maxSpinupValue, "Spn Max", 100, 500, 100, 500);
        }
        break;
      case 6:
        if(!speedLockedOut){
          renderGauge(minSpeedValue, "Spd Min", 0, 100, 0, maxSpeedValue);
        }
        break;
      case 7:
        if(!speedLockedOut){
          renderGauge(maxSpeedValue, "Spd Max", 0, 100, minSpeedValue, 100);
        }
        break;
      case 8:
        if(!speedLockedOut){
          renderPresetMenu(presetMenuIndex, "Load", presetMenuArray, presetMenuLength);
        }
        break;
      case 9:
        if(!speedLockedOut){
          renderPresetMenu(presetMenuIndex, "Save", presetMenuArray, presetMenuLength);
        }
        break;
      case 10:
        renderGauge(brightnessValue, "Bright ", 0, 100, 0, 100);
        break;
      case 11:
        renderSoundMenu();
        break;
      default:
        break;
    }
  }
  

  //look for rot switch press
  if(!digitalRead(menuBtnPin)){ 
    if(!menuBtnWasDown){

      if(liveKnobScrollMode){
        //tone(6,2000,50);
      }
      else{
        if(knobMenuIndex == 8 && presetMenuIndex > 0){
          loadPreset(presetMenuIndex); 
          presetMenuIndex = 0;
        }
        if(knobMenuIndex == 9  && presetMenuIndex > 0){
          savePreset(presetMenuIndex); 
          presetMenuIndex = 0; 
        }
      }

      liveKnobScrollMode = !liveKnobScrollMode;

      if(speedLockedOut && knobMenuIndex >= 4 && knobMenuIndex <= 9){
        liveKnobScrollMode = true;
      }
      
      uView.clear(PAGE);
      firstMenuRun = true;
      myEnc.write(0);
    }
    menuBtnWasDown = true;
  }
  else{
    menuBtnWasDown = false;
  }
  
}





void renderVoltMeter(){
  
  if(firstMenuRun){
    voltMeter->reDraw();
  }

  if(millis() > lastBatteryCheck + batteryCheckDelay){

    float v = (analogRead(voltMeterPin) * vPow) / 1024.0;
    float v2 = v / (r2 / (r1 + r2));

    v2 *= 10;
    int v2Int = (int)v2;
    v2 = (float)v2Int / 10;

    //uView.setCursor(34,0);
    //uView.print(v2);
    //tone(6, 2000, 20);

    batteryCheckSum -= batteryCheck[batteryCheckIndex];
    batteryCheck[batteryCheckIndex] = v2;
    batteryCheckSum += v2;
    batteryCheckIndex++;
    if(batteryCheckIndex >= batteryCheckLength){
      batteryCheckIndex = 0;
    }
    lastBatteryCheck = millis();
    
  }

  float voltLevel = batteryCheckSum / batteryCheckLength;
  voltMeter->setValue(voltLevel * 10);

  if(voltLevel < 11.0){
    if(lastBatAlarm + 3000 < millis()){
      batteryWarning();
      lastBatAlarm = millis();
    }
  }

  if(voltLevel < 10.9){
    if(lastBatAlarm + 1500 < millis()){
      batteryWarning();
      lastBatAlarm = millis();
    }
  }
  
  if(voltLevel < 10.8){
    if(lastBatAlarm + 1000 < millis()){
      batteryCritical();
      lastBatAlarm = millis();
    }
  }

  if(voltLevel < 10.7){
    while(true){
      digitalWrite(pusherEnablePin, LOW);
      flywheelESC.writeMicroseconds(1000);
      
      batteryCritical();
      delay(200);
    }
  }

  uView.setCursor(56,39);
  uView.print("B");
    
}

void batteryWarning(){
  tone(6, 2400);
  delay(140);
  tone(6, 4000);
  delay(140);
  tone(6, 1200);
  delay(200);
  noTone(6);
}

void batteryCritical(){
  tone(6, 2400, 140);
  delay(200);
  tone(6, 4000, 140);
  delay(200);
  tone(6, 2400, 140);
  delay(200);
  tone(6, 4000, 140);
}

void renderCounter(){

  uView.setCursor(34,0);
  
  if(counterValue < 0){
    counterValue = 0;
  }

  //if(counterValue <= 0){
  //  uView.print("EMPTY");
  //}
  //else{
    if(counterValue < 10){
      uView.print(" ");
    }
    if(magSizeValue < 10){
      uView.print(" ");
    }
    uView.print(counterValue);
    uView.print("/");
    uView.print(magSizeValue);
    uView.setFontType(0);
  //}
  
    
}

void renderLockIndicator(){

  uView.setCursor(34,0);
  uView.print("SLOCK");
  uView.setFontType(0);
    
}

void renderBurstMenu(){

  encoderChange += myEnc.read();
  myEnc.write(0);
  
  if(abs(encoderChange) >= 4){
    
    burstMenuIndex += encoderChange / 4;
    burstMenuIndex = constrain(burstMenuIndex, 0, 3);
    encoderChange = 0;
  }

  uView.setCursor(6,14);
  uView.print("Burst");

  uView.setFontType(1);
  uView.setCursor(18,26);
  uView.print(burstMenuArray[burstMenuIndex]);
  
  uView.display();
  firstMenuRun = false;
  uView.setFontType(0);
  
}

void renderSoundMenu(){

  encoderChange += myEnc.read();
  myEnc.write(0);
  
  if(abs(encoderChange) >= 4){
    
    soundMenuIndex += encoderChange / 4;
    soundMenuIndex = constrain(soundMenuIndex, 0, soundMenuLength - 1);
    encoderChange = 0;
  }

  uView.setCursor(6,14);
  uView.print("Sound");

  uView.setFontType(1);
  uView.setCursor(18,26);
  uView.print(soundMenuArray[soundMenuIndex]);
  
  uView.display();
  firstMenuRun = false;
  uView.setFontType(0);
  
}

void renderPresetMenu(int &menuIndex, String label, String menu[], int menuLength){

  encoderChange += myEnc.read();
  myEnc.write(0);
  
  if(abs(encoderChange) >= 4){
    
    menuIndex += encoderChange / 4;
    menuIndex = constrain(menuIndex, 0, menuLength - 1);
    encoderChange = 0;
  }

  uView.setCursor(10,14);
  uView.print(label);

  uView.setFontType(1);
  uView.setCursor(10,26);
  uView.print(menu[menuIndex]);
  
  uView.display();
  firstMenuRun = false;
  uView.setFontType(0);
  
}



void renderCounterMenu(){

  encoderChange += myEnc.read();
  myEnc.write(0);
  
  if(abs(encoderChange) >= 4){
    magSizeValue += encoderChange / 4;
    magSizeValue = constrain(magSizeValue, 1, 50);
    encoderChange = 0;
  }

  uView.setCursor(2,10);
  uView.print("Counter");

  uView.setFontType(1);
  uView.setCursor(10,26);

  if(magSizeValue < 10){
    uView.print(" ");
  }
  
  uView.print(magSizeValue);
  
  uView.display();
  firstMenuRun = false;
  uView.setFontType(0);
  
}


void renderKnobScrollMenu(){

  encoderChange += myEnc.read();
  myEnc.write(0);
  
  if(abs(encoderChange) >= 8){
    knobMenuIndex += encoderChange / 8;//was 4
    knobMenuIndex = constrain(knobMenuIndex, 0, knobMenuLength - 1);
    encoderChange = 0;
    if(soundMenuIndex == 0){
      tone(6,2000,10);
    }
  }

  uView.setCursor(0,0);
  uView.print("Mode");

  //uView.setFontType(1);
  uView.setCursor(8,26);
  uView.print(knobMenuArray[knobMenuIndex]);
  
  uView.display();
  firstMenuRun = false;
  uView.setFontType(0);
  
}


void renderGauge(int &gaugeValue, String label, int gaugeMin, int gaugeMax, int valueMin, int valueMax){

  mainGauge->setMinValue(gaugeMin);
  mainGauge->setMaxValue(gaugeMax);
  
  if(firstMenuRun){
    mainGauge->reDraw();
    myEnc.write(gaugeValue);
    firstMenuRun = false;
  }

  uView.setCursor(0,4);
  uView.print(label);
  
  gaugeValue = myEnc.read();
  if(gaugeValue > valueMax || gaugeValue < valueMin){
    gaugeValue = constrain(gaugeValue, valueMin, valueMax);
    myEnc.write(gaugeValue);
  }

  uView.setCursor(30,40);
  
  uView.print(gaugeValue);
  if(gaugeValue < 10){
    uView.print(" ");
  }
  if(gaugeValue < 100){
    uView.print(" ");
  }

  mainGauge->setValue(gaugeValue);
  uView.display();
}


void renderSplash(){

  uView.setFontType(1);
  uView.setCursor(6,14);
  uView.print("F");
  uView.display();
  delay(50);
  uView.print("D");
  uView.display();
  delay(50);
  uView.print("L");
  uView.display();
  delay(50);
  uView.print("-");
  uView.display();
  delay(50);
  uView.print("2");
  uView.display();
  delay(50);
  uView.print("X");
  uView.display();

  delay(400);
  
  uView.setFontType(0);
  
  delay(200);
  uView.clear(PAGE);
  uView.display();
  
}

/*
uint8_t bitmapTest [] = {
0x00, 0x00, 0xFC, 0x04, 0x04, 0x04, 0xC4, 0x44, 0x44, 0x44, 0x44, 0x44, 0x44, 0x44, 0x7C, 0x00,
0xFC, 0x04, 0x04, 0x04, 0xC4, 0x44, 0x44, 0x44, 0xC4, 0x84, 0x04, 0x0C, 0x18, 0x30, 0xE0, 0x00,
0x00, 0xFC, 0x04, 0x04, 0x04, 0xFC, 0x00, 0x00, 0x00, 0x00, 0x00, 0x00, 0x00, 0x00, 0x00, 0x00,
0x00, 0x00, 0x00, 0x00, 0x00, 0x00, 0x00, 0x00, 0x00, 0x00, 0x00, 0x00, 0x00, 0x00, 0x00, 0x00,
0x00, 0x00, 0xFF, 0x00, 0x00, 0x00, 0xC7, 0x44, 0x44, 0x44, 0x44, 0x44, 0x44, 0x44, 0x7C, 0x00,
0xFF, 0x00, 0x00, 0x00, 0xFF, 0x00, 0x00, 0x00, 0x00, 0x01, 0xFF, 0x00, 0x00, 0x00, 0xFF, 0x00,
0x00, 0xFF, 0x00, 0x00, 0x00, 0xFF, 0x00, 0x00, 0x00, 0x00, 0x00, 0x00, 0x00, 0x00, 0x00, 0x00,
0x00, 0x00, 0x00, 0x00, 0x00, 0x00, 0x00, 0x00, 0x00, 0x00, 0x00, 0x00, 0x00, 0x00, 0x00, 0x00,
0x00, 0x00, 0xFF, 0x00, 0x00, 0x00, 0xFF, 0x00, 0x00, 0x00, 0x00, 0x00, 0x00, 0x00, 0x00, 0x00,
0xFF, 0x00, 0x00, 0x00, 0x1F, 0x10, 0x10, 0x10, 0x18, 0x06, 0x83, 0xC0, 0x60, 0x30, 0x1F, 0x00,
0x00, 0xFF, 0x00, 0x00, 0x00, 0x1F, 0x10, 0x10, 0x10, 0x10, 0x10, 0x10, 0x10, 0xF0, 0x00, 0x00,
0x00, 0x00, 0x00, 0x00, 0x00, 0x00, 0x00, 0x00, 0x00, 0x00, 0x00, 0x00, 0x00, 0x00, 0x00, 0x00,
0x00, 0x00, 0x01, 0x01, 0x01, 0x01, 0x01, 0x00, 0x00, 0x00, 0x00, 0x00, 0x00, 0x00, 0x00, 0x00,
0x01, 0x01, 0x01, 0x01, 0x01, 0x01, 0x01, 0x01, 0x01, 0x01, 0x01, 0x80, 0x80, 0xC0, 0x60, 0x20,
0x20, 0x61, 0xC1, 0x81, 0x81, 0x01, 0x01, 0x01, 0xC1, 0xA1, 0x21, 0x21, 0xE1, 0x81, 0x00, 0x00,
0x00, 0x80, 0xE0, 0x20, 0x20, 0xE0, 0x60, 0x00, 0x00, 0x00, 0x00, 0x00, 0x00, 0x00, 0x00, 0x00,
0x00, 0x00, 0x00, 0x00, 0x00, 0x00, 0x00, 0x00, 0x00, 0x00, 0x00, 0x00, 0x00, 0x00, 0x00, 0x00,
0x00, 0x00, 0x00, 0x00, 0x00, 0x00, 0x00, 0x00, 0x00, 0x00, 0x00, 0x1F, 0x10, 0x10, 0x18, 0x0C,
0x84, 0xCC, 0x78, 0x00, 0xC1, 0x79, 0x0F, 0x00, 0x00, 0x07, 0xCC, 0x70, 0x00, 0x83, 0x86, 0x06,
0x43, 0xF1, 0x1C, 0x06, 0x03, 0x01, 0x00, 0x00, 0x00, 0x00, 0x00, 0x00, 0x00, 0x00, 0x00, 0x00,
0x00, 0x00, 0x00, 0x00, 0x00, 0x00, 0x00, 0x00, 0x00, 0x00, 0x00, 0x00, 0x00, 0x00, 0x00, 0x00,
0x00, 0x00, 0x00, 0x00, 0x00, 0x00, 0x00, 0x00, 0x00, 0x00, 0x00, 0x38, 0x2C, 0x26, 0x22, 0x23,
0x21, 0x20, 0x20, 0x23, 0x23, 0x22, 0x3E, 0x00, 0x3C, 0x23, 0x21, 0x30, 0x1C, 0x07, 0x07, 0x1C,
0x30, 0x23, 0x26, 0x3C, 0x30, 0x00, 0x00, 0x00, 0x00, 0x00, 0x00, 0x00, 0x00, 0x00, 0x00, 0x00
};
*/

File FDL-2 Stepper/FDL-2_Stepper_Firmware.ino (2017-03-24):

//FDL-2 Blaster Firmware
//Last Update: 2017-3-24

SYSTEM_MODE(SEMI_AUTOMATIC);

// Define the pins we're going to call pinMode on
int pusherSenseIn = D1;
int pusherStep = D4;
int stepperEnable = D6;
int stepperDir = D7;
int wifiSenseIn = RX;
int escPin = TX;

int speedSenseIn = A2;
int triggerSenseIn = A3;
int modeSenseIn = A4;

Servo flywheelESC;  // create servo object to control a ESC

int stepperWarmup = 80;

unsigned long disableMillis = millis();
unsigned long lastTriggerUp = 0;
bool firstRun = true;

const int minESCpower = 55;
const int maxESCpower = 160;
const int lowSpinupDelay = 240;
const int highSpinupDelay = 160;

const bool fixedMode = false;
const int fixedPower = 100;
const int fixedSpinup = 200;
const int fixedBurstCount = 100; 

String currentSettingsString = "55:160:240:160:0:100:0:100:200:100:2";
struct MySettings {
    int lowPower; 
    int highPower;
    int lowSpinup;
    int highSpinup;
    int lowROF;
    int highROF;
    int fixedMode;
    int fixedPower;
    int fixedSpinup;
    int fixedROF;
    int fixedBurstCount;
};
MySettings currentSettingsStruct = { 55, 160, 240, 160, 0, 100, 0, 100, 200, 100, 2 };


// This routine runs only once upon reset
void setup() {
    
  flywheelESC.attach(escPin);  // attaches pin to servo object
    
  // Initialize pins 
  // It's important you do this here, inside the setup() function rather than outside it or in the loop function.
  pinMode(pusherSenseIn, INPUT_PULLDOWN);
  pinMode(wifiSenseIn, INPUT_PULLDOWN);
  pinMode(speedSenseIn, INPUT);
  pinMode(modeSenseIn, INPUT);
  pinMode(triggerSenseIn, INPUT);
  pinMode(pusherStep, OUTPUT);
  pinMode(stepperEnable, OUTPUT);
  pinMode(stepperDir, OUTPUT);
  
  digitalWrite(stepperEnable, HIGH); // Turn off steppers (HIGH)
  digitalWrite(stepperDir, LOW);
  
  Particle.variable("settings", currentSettingsString);
  Particle.function("setsettings", settingsHandler);
  
  initSettings();
}

// This routine gets called repeatedly, like once every 5-15 milliseconds.
// Spark firmware interleaves background CPU activity associated with WiFi + Cloud activity with your code. 
// Make sure none of your code delays or blocks for too long (like more than 5 seconds), or weird things can happen.
void loop() {
  
    if(triggerDown()){
        
        //trigger down at boot, write max throttle to ESC to calibrate
        if(firstRun){
            while(digitalRead(triggerSenseIn) == HIGH){
                flywheelESC.writeMicroseconds(1860);
                delay(300);
            }
        
            flywheelESC.writeMicroseconds(1000);
            delay(1500);  
        }
        else{
            fireBrushlessLoop();
        }
    }
    else{
        flywheelESC.writeMicroseconds(1000);
    }
    
    if(digitalRead(wifiSenseIn) == HIGH){
      Particle.connect();
    }
    
    firstRun = false;
    
    if(millis() > disableMillis){
        digitalWrite(stepperEnable, HIGH);
    }
    
    delay(10);
}

boolean triggerDown(){
    return analogRead(speedSenseIn) > 20;
}

int readESCPower(){
    
    if(currentSettingsStruct.fixedMode > 0){
        return currentSettingsStruct.fixedPower;
    }
    else{
        int val = analogRead(speedSenseIn);
        return map(val, 0, 4094, currentSettingsStruct.lowPower, currentSettingsStruct.highPower);
    }
}

int getSpinup(){
    if(currentSettingsStruct.fixedMode > 0){
        return currentSettingsStruct.fixedSpinup;
    }
    else{
        int val = analogRead(speedSenseIn);
        return map(val, 0, 4094, currentSettingsStruct.lowSpinup, currentSettingsStruct.highSpinup);
    }
}

int getBurstCount(){
    if(currentSettingsStruct.fixedMode > 0){
        return currentSettingsStruct.fixedBurstCount;
    }
    else{
        int mVal = analogRead(modeSenseIn);
    
        if(mVal > 4000){
            return 1;
        }
        if(mVal < 1000){
            return 100;
        }
        if(mVal > 3000){
            return 2;
        }
        return 3;
    }
}

int getROF(){
    if(currentSettingsStruct.fixedMode > 0){
        return currentSettingsStruct.fixedROF;
    }
    else{
        int val = analogRead(triggerSenseIn);
        int rofPercent = map(val, 0, 4094, 0, 100);
    }
}


void fireBrushlessLoop(){
    
    unsigned long spinupEnd = millis() + getSpinup();
    
    //kick on flywheels
    int kickonSpeed = readESCPower();
    
    flywheelESC.write(kickonSpeed); 
    
    ////kick on steppers, wait for warmup
    digitalWrite(stepperEnable, LOW);
    
    //still holding the trigger?
    if(triggerDown()){
        
        //wait for spinup
        //if last trigger up less than a second ago, minimize delay
        if(lastTriggerUp != 0 && millis() - lastTriggerUp < 1000){
            spinupEnd = millis() + stepperWarmup;
        }
        
        while(millis() < spinupEnd){ delay(1); }
        
        int burstCount = getBurstCount(); 
        
        flywheelESC.write(readESCPower());
        
        while(triggerDown()){
            
            if(!spinPusherToSwitch()){
                reverseToPusherSwitch();
            }
            burstCount--;
            
            if(triggerDown() && burstCount > 0){
                
                flywheelESC.write(readESCPower()); 
            }
            else{
                brushlessPowerDown(1000);
                
                while(triggerDown()){
                    delay(1);
                }
                
                return;
            }
        }
        brushlessPowerDown(1000);
    }
    else{ 
        brushlessPowerDown(1000);
        return;
    }
    
}

void brushlessPowerDown(double millisToDisable){
    
    flywheelESC.writeMicroseconds(1000);
    
    //sets disable time for 1 sec
    disableMillis = millis() + millisToDisable;
    
    lastTriggerUp = millis();
}

bool spinPusherToSwitch(){
    
    //800 full spin
    //spin enough to let go of the switch (1/2 wayish)
    
    int rofPercent = getROF();
    
    int accStepsStart = map(rofPercent, 0, 100, 400, 80);
    
    int accStepsMid = 400 - accStepsStart;
    
    int accStartDelay = 460; 
    int accMidDelay = 150; 
    int accEndDelay = 110;
    
    StepRange(pusherStep, accStartDelay, accMidDelay, accStepsStart);
    StepRange(pusherStep, accMidDelay, accEndDelay, accStepsMid);

    for(int stepIndex = 0; stepIndex < 500; stepIndex++){
       StepRange(pusherStep, accEndDelay, accEndDelay, 1); 
       
       if(digitalRead(pusherSenseIn) == HIGH){
           return true;
       }
    }
    
    return false;
}

bool reverseToPusherSwitch(){
    
    digitalWrite(stepperDir, HIGH);
    
    for(int stepIndex = 0; stepIndex < 1000; stepIndex++){
        
        if(digitalRead(pusherSenseIn) == LOW){
           StepDelay(pusherStep, 400, 1);
        }
        else{
            break;
        }
        
    }
    
    digitalWrite(stepperDir, LOW);
    
    return digitalRead(pusherSenseIn) == HIGH;
}
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

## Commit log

2016-12-18 Initial commit STL, Firmware, BOM
    [FDL-2_Barrel_Cap.stl, FDL-2_Barrel_Main.stl, FDL-2_ESC_Wire_Cap_L.stl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]
2016-12-24 Shortening spinner bushing
    [FDL-2_Spinner_Bushing.stl]
2016-12-24 Extending front edges to meet outer guard.
    [FDL-2_Handle_Guard_Inner.stl]
2016-12-24 Loosening slots for better fit
    [FDL-2_PCB_Mount.stl]
2016-12-24 Adding wire guard across top to keep trigger wire away from pusher mech
    [FDL-2_Handle.stl]
2016-12-24 Updated magwell to fit Buzz Bee mags,
    [FDL-2_Magwell.stl]
2017-01-16 Updating rear plate stl to accommodate longer 5pin connector housing.
    [FDL-2_Rear_Plate.stl]
2017-03-10 Adding FDL-2 wiring diagram
2017-03-10 Removing wiring diagram jpg
2017-03-10 Adding high crush flywheel stl
    [FDL-2_Flywheel_x2_High_Crush.stl]
2017-03-14 Fixing artifacts on main barrel
    [FDL-2_Barrel_Main.stl]
2017-03-26 Updated: Main barrel - remove mesh errors Mag release - bigger button, better fit Rear plate - adjusted pusher guide lower Spinner - lengthened collar Handle guards - Better positive close and fit
    [FDL-2_Barrel_Main.stl, FDL-2_Flywheel x2 Medium Crush.stl, FDL-2_Handle_Guard_Inner.stl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]
2017-05-10 Adding new FDL-2 wiring diagram to match the new CTRL v1.1 PCB.
2017-05-19 Adding FDL-2+ files
    [FDL-2+_Electronics_Cover.stl, FDL-2+_Rear_Plate.stl, FDL-2+_Rear_Plate_Cap_Front.stl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]
2017-12-05 File reorg for 2X
    [FDL-2+_Electronics_Cover.stl, FDL-2+_Mode_Knob.stl, FDL-2+_Nameplate.stl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]
2017-12-05 Removing old files
    [FDL-2+_Electronics_Cover.stl, FDL-2+_Rear_Plate.stl, FDL-2+_Rear_Plate_Cap_Front.stl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]
2018-03-24 Adding 2X wiring diagram
2021-11-18 Add 2x bom and pcb eagle files
    [FDL-2 DCP.brd, FDL-2 DCP.sch, FDL-2X CTRL.brd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]

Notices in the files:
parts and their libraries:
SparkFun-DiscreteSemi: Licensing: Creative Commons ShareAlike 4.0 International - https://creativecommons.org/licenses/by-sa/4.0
